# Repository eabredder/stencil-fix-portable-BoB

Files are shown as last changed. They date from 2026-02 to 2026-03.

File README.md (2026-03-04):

# **Stencil Fix Portable — BoB v.03 - PCB**

A purpose-built **drop‑in PCB** for the **Stencil Fix Portable** vacuum stencil holder. This board replaces the original perfboard wiring with a compact, repeatable assembly, eliminating soldering any wires using common connectors using an **Adafruit QtPy SAMD21 (QtPy M0)**, a **B10K potentiometer** for vacuum control, a **128×32 SSD1306 OLED** for status, and a **30A ESC** driving an **A2212 BLDC motor**. The CAD files in this repository are updated to fit these changes. You can still use this with the original Stencil Fix Portable design and components, you may need to adjust the range of motor control (µs), arming procedure, without the OLED. The PCB outline is 80mm x 20mm, matching common perfboard layout and mounting.

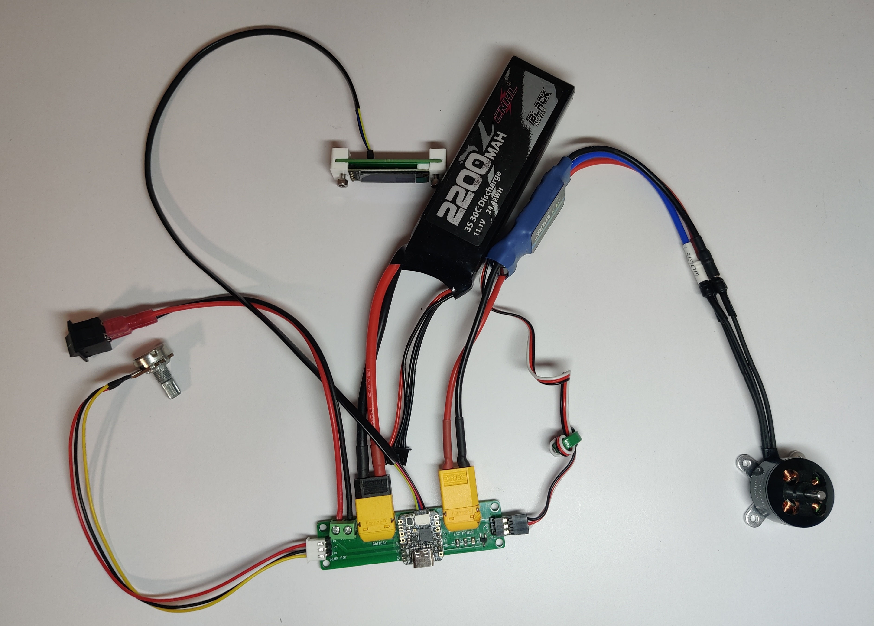
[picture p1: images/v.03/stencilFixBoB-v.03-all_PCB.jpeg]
StencilFix BoB v.03 Connected Components


<!--![StencilFix BoB v.03 3D View](images/v.03/3DView-Components-v.03.png)-->

This project is intended to be used with the original Stencil Fix Portable mechanical design and overall concept from the upstream project: [**Stencil Fix Portable** by scheffield](https://github.com/scheffield/stencil-fix-portable). Our updates reflect using more commonly sourced hardware, simplifying the build, and lower cost components. See BOM for updated components and design decisions.

---

## **Highlights / Features**

- **Drop-in replacement PCB** for the Stencil Fix Portable electronics
- **Cooperative Multitasking** providing simple scheduler and tasks using [TaskScheduler](https://github.com/arkhipenko/TaskScheduler)
- [**QtPy SAMD21** microcontroller](https://github.com/adafruit/Adafruit-QT-Py-PCB/blob/master/README.md)
- **Vacuum control** via 10K potentiometer → mapped to ESC PWM (servo µs)
- **5V input from ESC**: 
-  - No need for buck-boost
-  - BAT54 Diode protection
- **OLED UI (128×32 SSD1306)**:
  - Vacuum % bar
  - Battery % bar (with low/critical blinking label)
  - Fan state (ON/OFF)
  - Auto **screen dim after 30 seconds** inactivity
- **Battery SoC estimation** via voltage divider (scaled for **3S LiPo**)
- **Input smoothing** using a one-pole low-pass filter (reduces “twitchy” response)
- **Onboard NeoPixel UX**:
  - Arming/breathing animation
  - Hue reflects potentiometer
  - Low-battery dimming
  - Critical-battery blink
- **XT60 Connectors** standardized connections for RC batteries and ESCs, reduce connector/wiring inside
- **Power Switch** simplified through screw terminals
- **80x20mm Outline**  with 3.2mm Mounting Holes to fit multiple screw types and heat set threaded inserts and drop-in to original design

---

## **Hardware Overview**

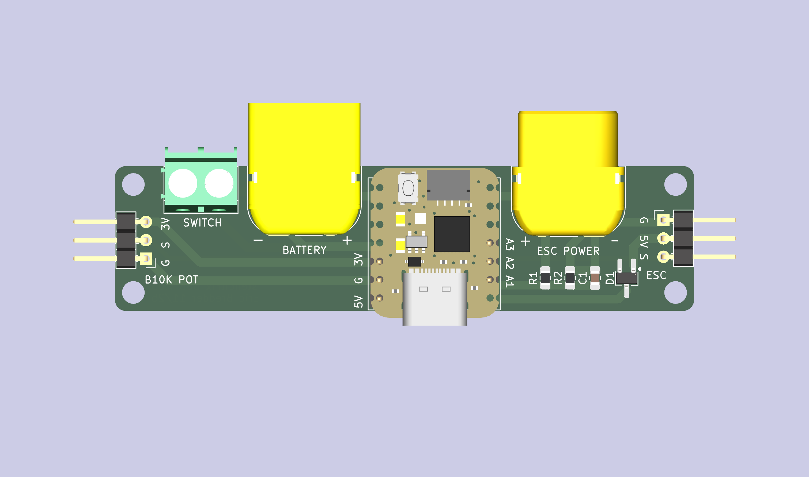
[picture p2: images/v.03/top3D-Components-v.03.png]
 

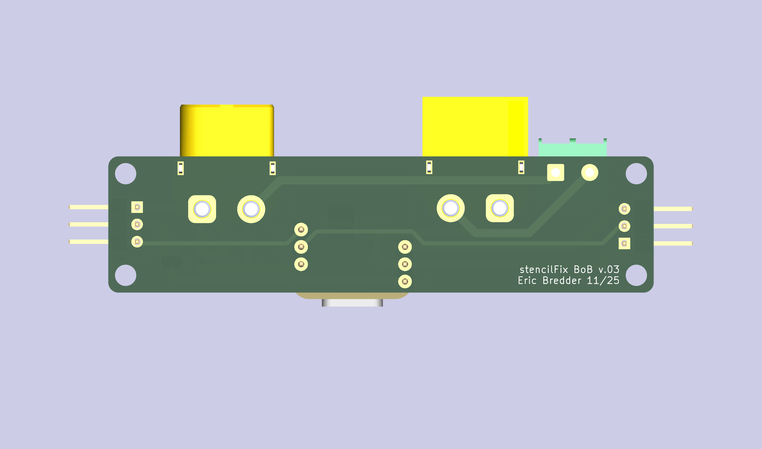
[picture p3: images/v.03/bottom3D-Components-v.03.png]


### **PCB Components**
- MCU
  - U1: [Adafruit QtPy SAMD21 (QtPy M0)](https://www.adafruit.com/qtpy)
- Battery sense & filtering
  - R1: [300kΩ 0805 Resistor](https://a.co/d/0bcWREO8)
  - R2: [100kΩ 0805 Resistor](https://a.co/d/0bcWREO8)
  - C1: [100nF 0805 Capacitor](https://a.co/d/0i44cuZE)
- Protection
  - D1: [BAT54 Schottky Diode SOT-23-3](https://a.co/d/0dFgMzRd)
- Connectors
  - J5, ESC Power: [XT60 Male](https://a.co/d/0fRPskBY)
  - J2, ESC UBEC: [2.54mm Male Right Angle](https://a.co/d/08ONmiCH) - 3 pin
  - J3, Battery: [XT60 Female](https://a.co/d/0fRPskBY)
  - J4, Power Switch: [5.08mm Screw Terminal Block](https://a.co/d/0d4A6ITm) - 2 pin
  - J1, Potentiometer: [2.54mm Male Right Angle](https://a.co/d/08ONmiCH) - 3 pin
  - U1, MCU Header: [2.54 Male Straight](https://a.co/d/08ONmiCH) - 3 pin (2x)
    
### **External Hardware**
- Control: [B10K (10KΩ) Linear Potentiometer](https://a.co/d/0iVrtQ9j)
- Motor: [A2212 1400kV BLDC Motor](https://a.co/d/0cnJZqye)
- ESC: [30A ESC with 5V BEC](https://a.co/d/0eS2Lal8)
- Battery: [3S LiPo (nominal 11.1V, max 12.6V)](https://a.co/d/00FffIhA)
- Switch: [SPST - 19.2mm x 12.7mm](https://a.co/d/03Vc4zIX)
- Display: 128×32 SSD1306 I2C OLED (0x3C): [OLED Only (Solder or add backpack)](https://a.co/d/053kOUIJ) OR [Adafruit 4440 (Stemma QT)](https://www.adafruit.com/product/4440)
- Wire (better for switch): [18AWG Silicone Wire](https://a.co/d/00WXGGEn)
- Qwiic/Stemma QT Cable (for display): [200mm Stemma QT Cable](https://www.adafruit.com/product/4401) OR [150mm Stemma QT w/ Headers Cable](https://www.adafruit.com/product/4209)

### **Charging**
- Extension cable: [200mm JST-XH Balance Plug Extension](https://a.co/d/07cr4UUC)
- LiPo Charger: [B3 Balance Charger - 3S XH3P Plug](https://a.co/d/02X7mcL8)

## **Electrical Design Notes**

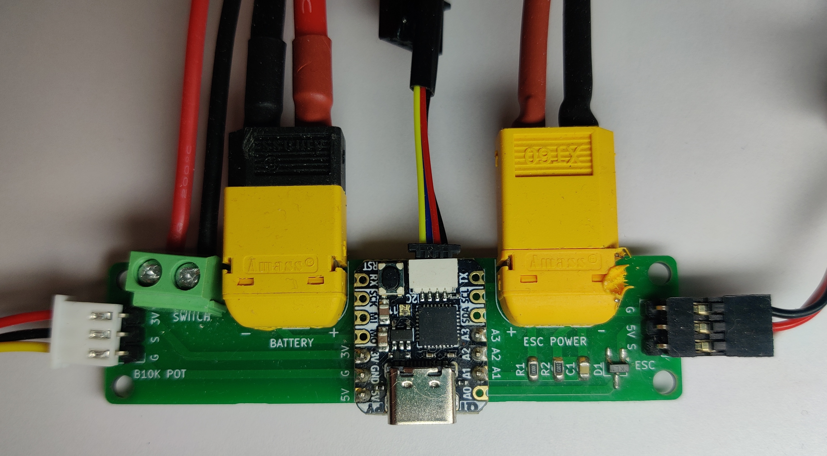
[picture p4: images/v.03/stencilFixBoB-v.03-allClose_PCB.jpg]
StencilFix BoB v.03 3D View


### **Schematic**
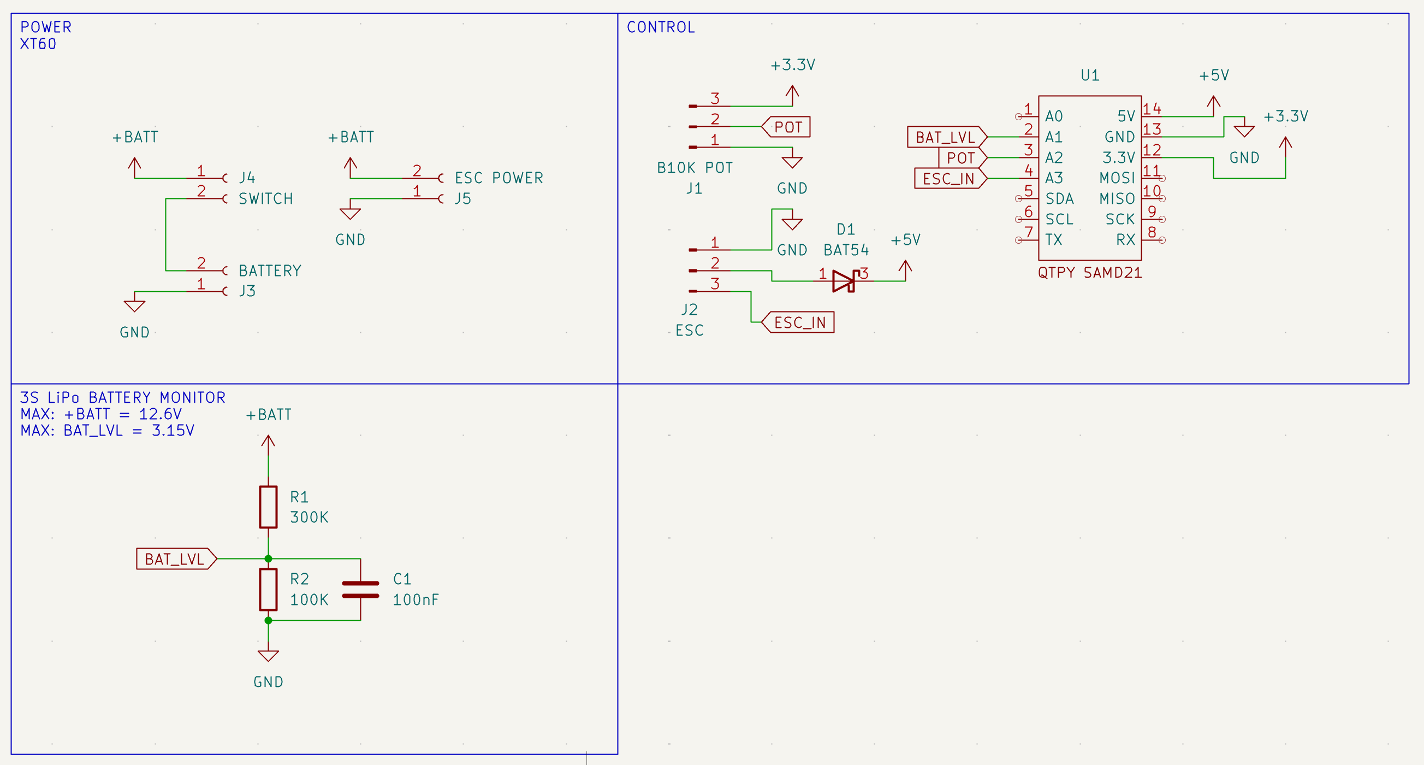
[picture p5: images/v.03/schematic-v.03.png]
StencilFix BoB v.03 KiCad Schematic


### **3S LiPo Battery Monitor/Filter (safe for 3.3V ADC)**

**R1** = 300kΩ, **R2** = 100kΩ
```text
R2 / (R1 + R2) = 100kΩ / 400kΩ = 0.25
```

So at 12.6V max, ADC max voltage:
```text
12.6V × 0.25 = 3.15V
```

**C1** = 100nF (from BAT_LVL to GND as simple RC filter)

### **ESC 5V Protection (Schottky diode)**
**D1** = BAT54 Schottky diode on the ESC’s 5V UBEC rail - used to prevent reverse-current/back-powering conditions between supplies. Expect a small forward voltage drop, typically a few hundred mV depending on load.

### **Connectors / Wiring**

**J3** — BATTERY (XT60, female on PCB) - Connect 3S LiPo here

**J5** — ESC POWER (XT60, male on PCB) - Connect ESC power input here

**J4** — SWITCH (2-pin screw terminal block) - Inline with the battery positive path (rocker switch pigtails)

**J2** — ESC (3-pin)
- ESC_IN PWM signal to ESC (servo µs)
- +5V from ESC UBEC (through diode to board +5V rail)
- GND

**J1** — B10K POT (3-pin)
- 3.3V
- POT, wiper input
- GND

**I2C OLED**
- SDA / SCL from the QtPy STEMMA QT Connector
- Address: 0x3C
- Power: 3.3V

### **SAMD21 Pin Mapping**

| **Pin**  | **MCU Function** | **Schematic** | **Notes** |
|---|---|---|---|
| A1 | Battery Level Input | BAT_LVL | 3.15V Max Voltage Divider for Battery SoC |
| A2 | Potentiometer Input | POT | 12-bit ADC Potentiometer Scaled Input for Control |
| A3 | PWM Signal Output | ESC_IN | PWM Output for ESC Control |
| 5V | 5V Power In | +5V | 5V Power Input from Schottky Diode/ESC UBEC |
| GND  | Ground | GND | Common Ground |
| 3.3V | 3.3V Power Out | +3.3V | 3.3V Power Output for Potentiometer and OLED |

Uses PIN_NEOPIXEL [(built-in QtPy NeoPixel support)](https://learn.adafruit.com/adafruit-qt-py/neopixel-blink)

## **Firmware Notes**
**ESC arming**

On boot, ESC is held at 1000 µs for 2 seconds, then control is enabled. While not armed, NeoPixel shows an amber “breathing” animation.

**Pot → PWM mapping**

ADC reads at 12-bit (0..4095), Mapped to 1100..1400 µs (then low-pass filtered), If filtered value < 1110 µs, output floors to 1000 µs (fan off), Vacuum % shown as: 1100..1400 µs → 0..100%

**Display**

Vac bar with % (top row), Bat bar with % (second row, “Bat” blinks at low/critical), Bottom row: Fan: ON/OFF, Screen dims after 30 seconds of inactivity and wakes on pot movement or fan state change.

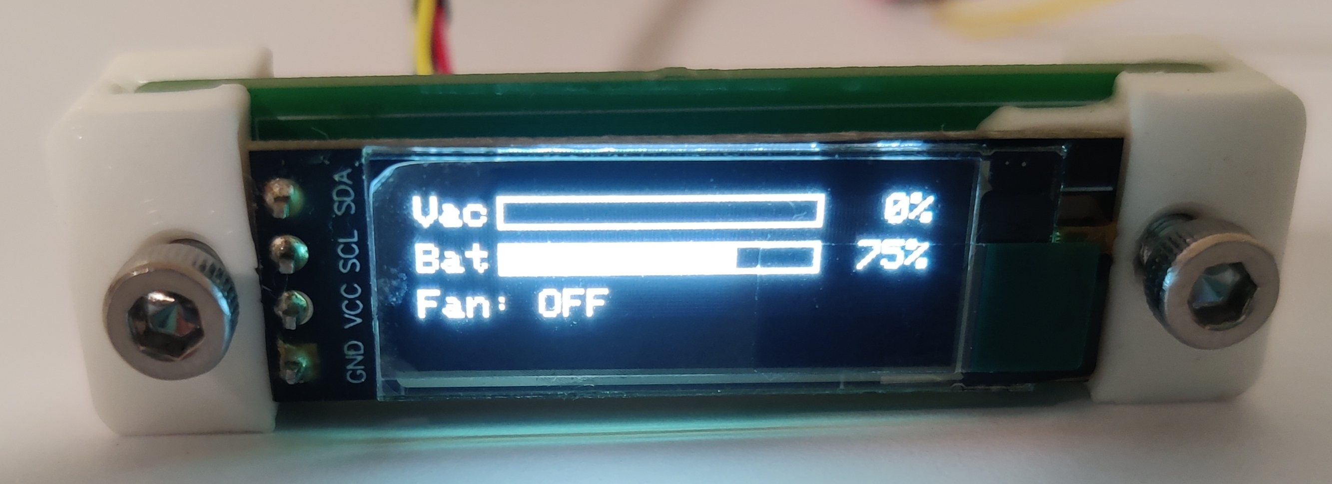
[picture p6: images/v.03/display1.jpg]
StencilFix BoB v.03 Display Off
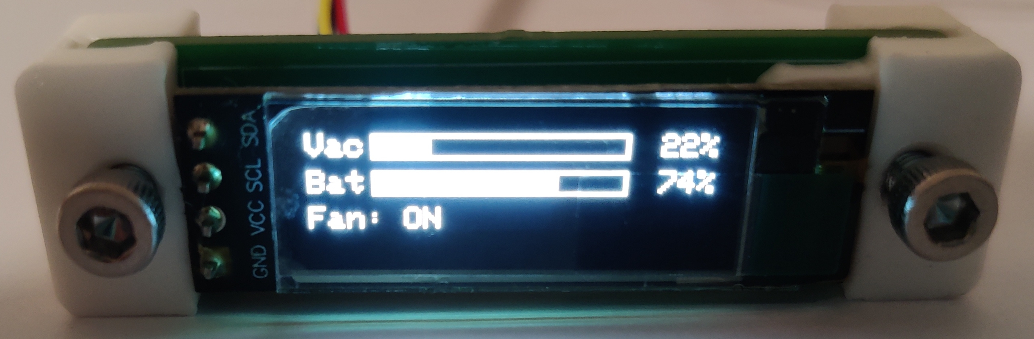
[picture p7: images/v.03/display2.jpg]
StencilFix BoB v.03 Display On
  

**Battery**

Battery SoC % computed and smoothed with moving averages:
```text
vmin = 9.0V
vmax = 12.6V
```

### **Arduino Libraries**
**Community**:
- [TaskScheduler](https://github.com/arkhipenko/TaskScheduler)
- [Adafruit_NeoPixel](https://github.com/adafruit/Adafruit_NeoPixel)
- [Servo](https://github.com/arduino-libraries/Servo)
- [Adafruit_GFX](https://github.com/adafruit/Adafruit-GFX-Library)
- [Adafruit_SSD1306](https://github.com/adafruit/Adafruit_SSD1306)
- [movingAvg](https://github.com/JChristensen/movingAvg/tree/master)

**Included**:
- lib/BatteryMeter.h [adapted from ESP Battery Shield](https://github.com/inf0matics/esp-battery-shield/tree/main/lib/BatteryMeter)

### **Attribution / Inspiration**

Stencil Fix Portable upstream project by scheffield (mechanical + concept reference). [Stencil Fix Portable](https://github.com/scheffield/stencil-fix-portable)

Battery meter approach referenced from ESP-Battery-Shield by inf0matics (voltage divider / ADC math concept). [ESP Battery Shield](https://github.com/inf0matics/esp-battery-shield/tree/main/lib/BatteryMeter)

**License:** [GNU General Public License v3.0](https://www.gnu.org/licenses/gpl-3.0.en.html)

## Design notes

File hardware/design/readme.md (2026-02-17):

[4600 QTPy.step - Adafruit](https://github.com/adafruit/Adafruit_CAD_Parts/tree/main/4600%20QT%20Py)

[AMASS XT60PW Connectors -  Anton Kolomeytsev](https://grabcad.com/library/xt60pw-and-xt60-dc-connectors-1)

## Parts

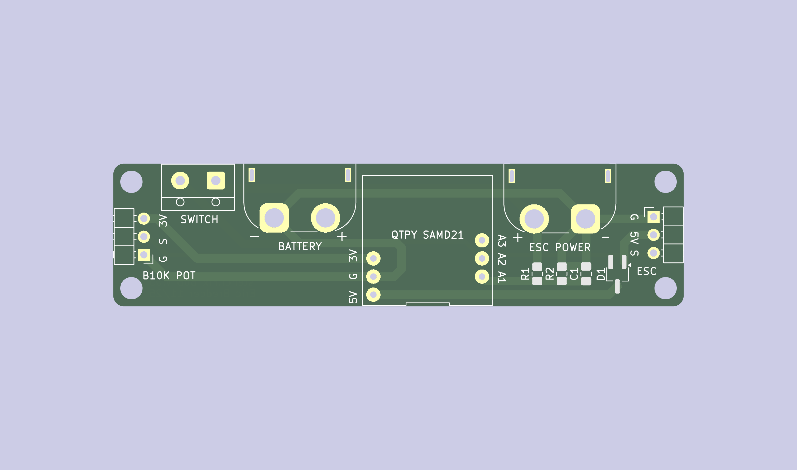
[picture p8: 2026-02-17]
images/v.03/top3D-noComponents-v.03.png

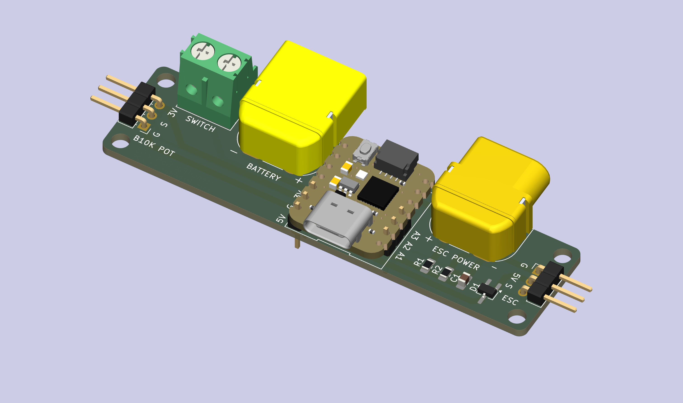
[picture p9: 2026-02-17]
images/v.03/3DView-Components-v.03.png

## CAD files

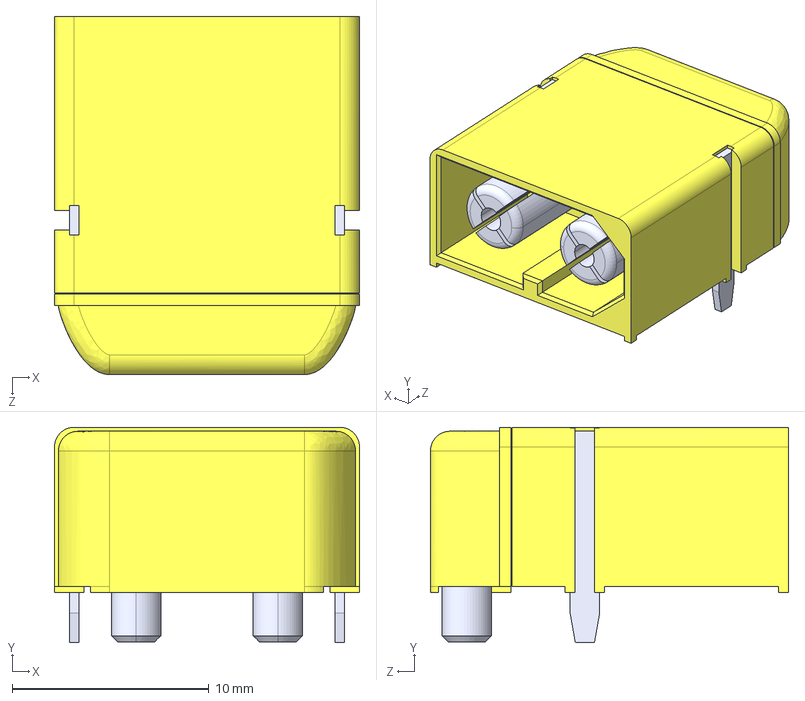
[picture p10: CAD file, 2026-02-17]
hardware/design/XT60PW-M--3DModel-STEP-269445.STEP
15.5 x 11.0 x 18.2 mm

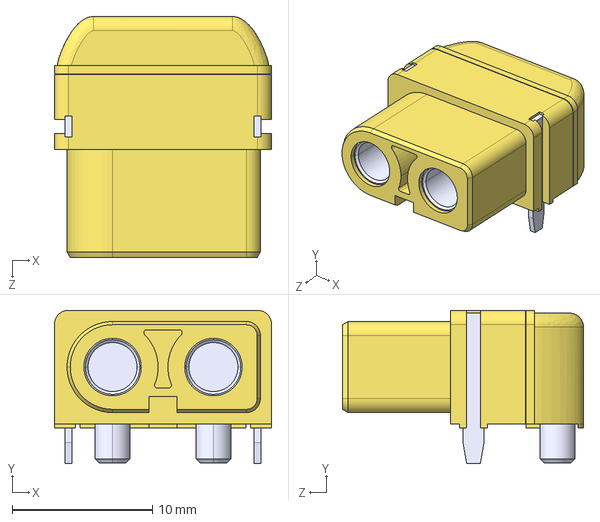
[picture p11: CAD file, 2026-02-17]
hardware/design/XT60PW-F--3DModel-STEP-510211.STEP
15.5 x 10.9 x 17.2 mm

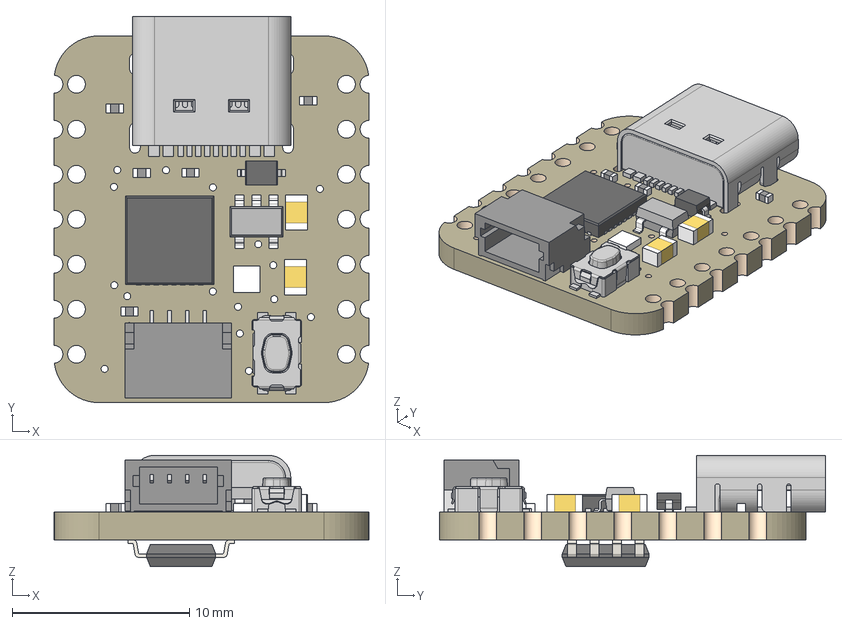
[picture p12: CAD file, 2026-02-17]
hardware/design/4600 QTPy.step
17.8 x 21.8 x 6.28 mm
Board
10uF x 2
reset
ATSAMD21E
TPB1,27
5.1K x 5
USB TYPE C
STEMMA_I2C_QTSKINNY
AP2112K-3.3
WS2812B_SK6805_1515
NSR0320
SOIC8_150MIL

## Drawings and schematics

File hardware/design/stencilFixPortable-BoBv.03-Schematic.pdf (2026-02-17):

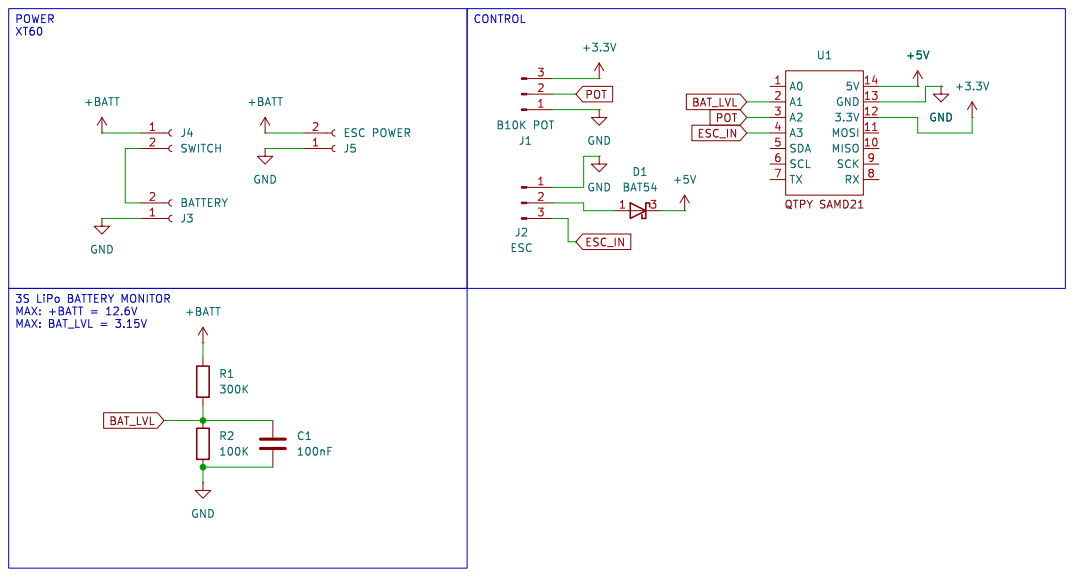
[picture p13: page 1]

+BATT GND J4SWITCH J5ESC POWER 2 1 J3BATTERY 1

3S LiPo BATTERY MONITOR MAX: +BATT = 12.6V MAX: BAT_LVL = 3.15V

Id: 1/1 Title: Stencil Fix Portable - BoB

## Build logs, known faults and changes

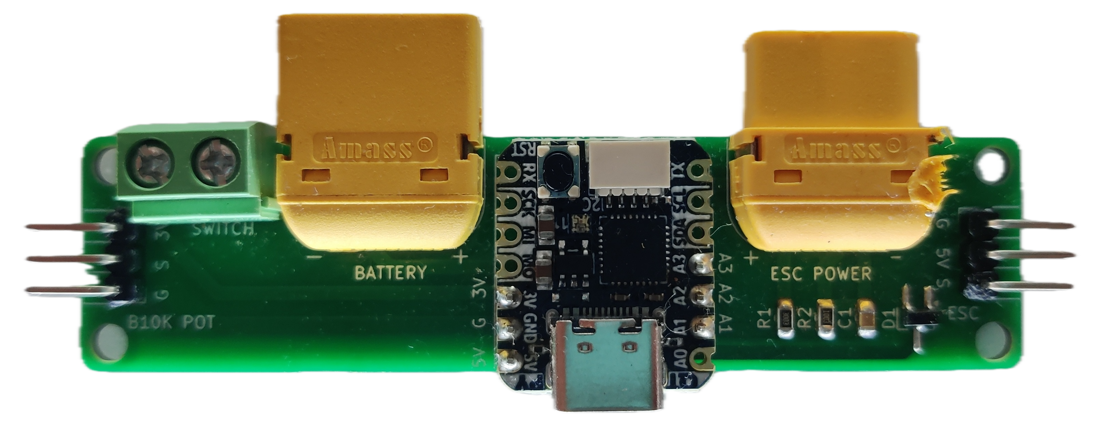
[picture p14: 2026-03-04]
images/v.03/stencilFixBoB-v.03-componentsTop_PCB.png

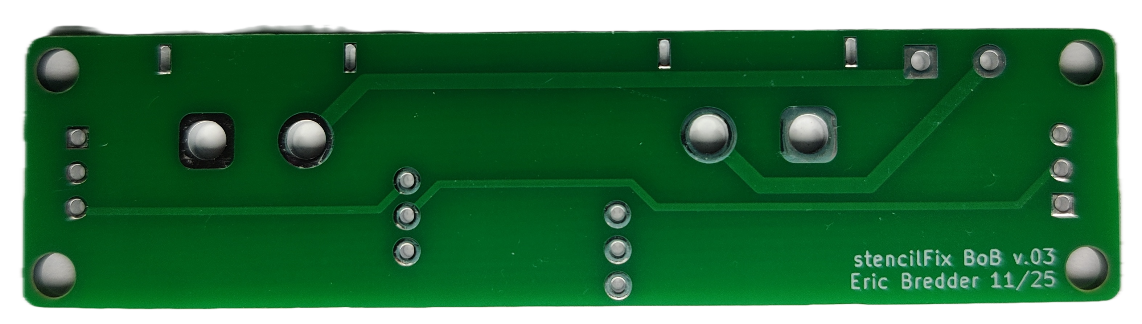
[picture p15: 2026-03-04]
images/v.03/stencilFixBoB-v.03-bottom_PCB.png

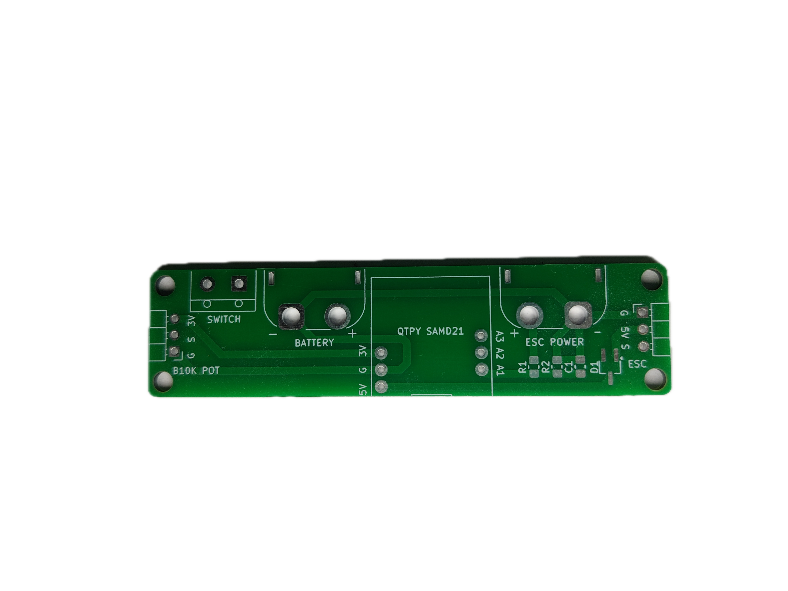
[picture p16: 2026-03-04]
images/v.03/stencilFixBoB-v.03-top_PCB.png

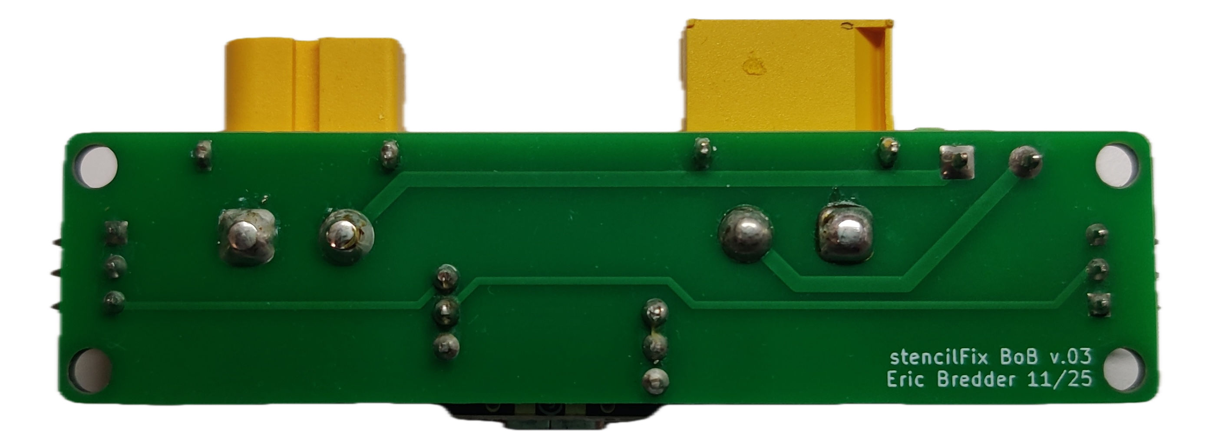
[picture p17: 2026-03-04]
images/v.03/stencilFixBoB-v.03-allBottom_PCB.png

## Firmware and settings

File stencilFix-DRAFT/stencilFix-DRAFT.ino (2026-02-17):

// ==== Battery meter from https://github.com/thespielplatz/esp-battery-shield ====

#include <Arduino.h>
#include <TaskScheduler.h>

#include <Adafruit_NeoPixel.h>
#include <Servo.h>

// Display
#include <Wire.h>
#include <Adafruit_GFX.h>
#include <Adafruit_SSD1306.h>

// Sensors
#include "BatteryMeter.h"
#include <movingAvg.h>

// ---------------------- Low-pass filter ----------------------
class LowPass {
  public:
    explicit LowPass(float RCus) : _RCus(RCus) {}
    float step(float x) {
      unsigned long now = micros();
      if (_lastMicros == 0) {
        _lastMicros = now;
        _y = x;
        return _y;
      }
      unsigned long dt = now - _lastMicros; // microseconds
      _lastMicros = now;
      // Standard one-pole: alpha = dt / (RC + dt)
      float alpha = (float)dt / (_RCus + (float)dt);
      _y += alpha * (x - _y);
      return _y;
    }
    void reset(float x) {
      _y = x;
      _lastMicros = micros();
    }
  private:
    float _y = 0.0f;
    float _RCus;                 // time constant in microseconds
    unsigned long _lastMicros = 0;
};

// ---------------------- OLED ----------------------
#define SCREEN_WIDTH 128
#define SCREEN_HEIGHT 32
#define SCREEN_ADDRESS 0x3C
Adafruit_SSD1306 display(SCREEN_WIDTH, SCREEN_HEIGHT, &Wire);

// ---------------------- Battery ----------------------
movingAvg avgBatt(22);
const int batteryPin = A1;
const float R1 = 300000.0;
const float R2 = 100000.0;
const float vmin = 9.0;
const float vmax = 12.6;
BatteryMeter* batteryMeter = new BatteryMeter(R1, R2, batteryPin, vmin, vmax);

// ---------------------- NeoPixel ----------------------
#define NUMPIXELS 1
Adafruit_NeoPixel pixels(NUMPIXELS, PIN_NEOPIXEL, NEO_GRB + NEO_KHZ800);

// ----- Onboard NeoPixel power & brightness policy -----
const uint8_t BRIGHT_ARMED   = 32;  // arming animation
const uint8_t BRIGHT_NORMAL  = 24;  // default after arming
const uint8_t BRIGHT_LOW     = 10;  // low battery dim
const uint8_t BRIGHT_CRIT    = 4;   // critical battery dim/blink
const int     BATT_LOW_PCT   = 25;  // thresholds for dimming
const int     BATT_CRIT_PCT  = 10;  // thresholds for blinking

// ---------------------- Servo / ESC ----------------------
Servo servo;

// ---------------------- Pins ----------------------
const int potPin   = A2;   // potentiometer
const int servoPin = A3;   // ESC signal (QtPy M0 supports this)

// ---------------------- Filters & State ----------------------
// Original RC = 40us; for stronger smoothing try 50–150ms (e.g., 100000 us).
LowPass lowPass(100000.0f);

// Shared state
volatile int      g_rawPot       = 0;      // 0..4095
volatile int      g_servoUs      = 1100;   // clamped microseconds for ESC
volatile int      g_vacuumPct    = 0;      // 0..100
volatile int      g_battPct      = 0;      // 0..100
volatile float    g_battVoltage  = 0.0f;   // volts
volatile uint16_t g_pixelHue     = 0;      // 0..65535
volatile bool     g_escArmed     = false;  // becomes true after arming delay

// ---------- Screen Dimming ----------
unsigned long lastActivityTime = 0;
const unsigned long screenDimTimeout = 30000;  // 30 seconds
bool screenDimmed = false;

// ---------------------- Scheduler ----------------------
Scheduler runner;

// ---------- Forward declarations ----------
void taskReadInputsCb();
void taskServoCb();
void taskPixelCb();
void taskBatteryCb();
void taskDisplayCb();
void taskSerialCb();
void taskArmEscCb();

void drawBar(int x, int y, int width, int height, int pct);
void printRightAligned(const String& s, int xRight, int y);
bool blinkState(unsigned long periodMs);

// Periods — responsive but light
Task taskReadInputs (5   /*ms*/, TASK_FOREVER, &taskReadInputsCb, &runner, false);
Task taskServo      (10  /*ms*/, TASK_FOREVER, &taskServoCb     , &runner, false);
Task taskPixel      (20  /*ms*/, TASK_FOREVER, &taskPixelCb     , &runner, false);
Task taskBattery    (250 /*ms*/, TASK_FOREVER, &taskBatteryCb   , &runner, false);
Task taskDisplay    (200 /*ms*/, TASK_FOREVER, &taskDisplayCb   , &runner, false);
Task taskSerial     (1000/*ms*/, TASK_FOREVER, &taskSerialCb    , &runner, false);

// Non-blocking ESC arming (hold 1000us for 2s, then allow control)
Task taskArmEsc     (2000/*ms*/, TASK_ONCE,   &taskArmEscCb     , &runner, false);

// ---------------------- Setup ----------------------
void setup() {
  Serial.begin(115200); // SAMD21 handles higher baud nicely

  // SAMD21 ADC: 12-bit range 0..4095
  analogReadResolution(12);

  // Display
  if (!display.begin(SSD1306_SWITCHCAPVCC, SCREEN_ADDRESS)) {
    Serial.println(F("SSD1306 allocation failed"));
    for(;;) { /* stop here if OLED not present */ }
  }
  display.clearDisplay();
  display.setTextColor(SSD1306_WHITE, SSD1306_BLACK);
  display.setRotation(0);
  display.display();

  // Battery smoothing
  avgBatt.begin();

  // Onboard NeoPixel (QtPy M0 has PIN_NEOPIXEL; NEOPIXEL_POWER may or may not exist)
  #if defined(NEOPIXEL_POWER)
    pinMode(NEOPIXEL_POWER, OUTPUT);
    digitalWrite(NEOPIXEL_POWER, HIGH);
  #endif
  pixels.begin();
  pixels.setBrightness(BRIGHT_NORMAL); // start conservative
  pixels.clear();
  pixels.show();

  // IO
  pinMode(potPin, INPUT);
  pinMode(batteryPin, INPUT);

  // Servo / ESC
  servo.attach(servoPin, 1100, 1900); // SAMD21 Servo lib works on this pin

  // Initialize the low-pass to the current mapped value to avoid a jump
  int pot0 = analogRead(potPin);
  int initialUs = map(pot0, 0, 4095, 1100, 1400);
  lowPass.reset(initialUs);

  // Initialize activity timer & full brightness
  lastActivityTime = millis();
  screenDimmed = false;
  display.ssd1306_command(SSD1306_SETCONTRAST);
  display.ssd1306_command(255);

  // Start tasks
  taskReadInputs.enable();
  taskServo.enable();
  taskPixel.enable();
  taskBattery.enable();
  taskDisplay.enable();
  taskSerial.enable();

  // Start non-blocking ESC arming
  taskArmEsc.enable(); // after 2000ms it will set g_escArmed = true
}

// ---------------------- Loop ----------------------
void loop() {
  runner.execute(); // cooperative dispatcher
}

// ---------------------- Helper drawing & UI functions ----------------------

// Generic compact progress bar
void drawBar(int x, int y, int width, int height, int pct) {
  pct = constrain(pct, 0, 100);
  display.drawRect(x, y, width, height, SSD1306_WHITE);
  int fillWidth = map(pct, 0, 100, 0, width - 2);
  if (fillWidth > 0) {
    display.fillRect(x + 1, y + 1, fillWidth, height - 2, SSD1306_WHITE);
  }
}

// Right-align small text (size=1) to an xRight column
void printRightAligned(const String& s, int xRight, int y) {
  // Each character at size=1 is ~6px wide in the default GFX font
  int textWidth = s.length() * 6;
  int x = xRight - textWidth + 1;  // +1 to balance outline pixels
  if (x < 0) x = 0;
  display.setCursor(x, y);
  display.print(s);
}

// Non-blocking blink state helper
bool blinkState(unsigned long periodMs) {
  return (millis() / periodMs) % 2 == 0;
}

// ---------------------- Task Callbacks ----------------------

// Sample pot, LPF, compute servo µs and vacuum %
void taskReadInputsCb() {
  int pot = analogRead(potPin);   // 12-bit on SAMD21
  g_rawPot = pot;

  // Map pot to 1100..1400us target, then low-pass
  int targetUs = map(pot, 0, 4095, 1100, 1400);
  int filtered = (int) lowPass.step((float)targetUs);

  // Original behavior: floor to 1000 if <1110
  if (filtered < 1110) filtered = 1000;

  // Clamp safe ESC range
  filtered = constrain(filtered, 1000, 1400);
  g_servoUs = filtered;

  // Vacuum percentage from 1100..1400 → 0..100
  int pct = map(filtered, 1100, 1400, 0, 100);
  g_vacuumPct = constrain(pct, 0, 100);

  // ---------- Inactivity detection for screen dimming ----------
  static int  lastPot    = -1;
  static bool lastFanOn  = false;
  bool fanOn = (g_vacuumPct > 0 && g_escArmed);

  if (pot != lastPot || fanOn != lastFanOn) {
    lastActivityTime = millis();
    if (screenDimmed) {
      // Restore brightness immediately on activity
      display.ssd1306_command(SSD1306_SETCONTRAST);
      display.ssd1306_command(255);  // full brightness
      screenDimmed = false;
    }
  }
  lastPot   = pot;
  lastFanOn = fanOn;
}

// Drive the servo/ESC (respect arming)
void taskServoCb() {
  int outUs = g_escArmed ? g_servoUs : 1000;
  servo.writeMicroseconds(outUs);
}

// Onboard NeoPixel policy:
// - Critical battery: red blink (1 Hz)
// - Not armed: breathing amber
// - Armed: hue by pot (240°..360°), brightness dimmed on low battery
void taskPixelCb() {
  uint32_t now = millis();

  // Critical battery: slow red blink (1 Hz, 500ms on/500ms off)
  if (g_battPct <= BATT_CRIT_PCT) {
    bool on = ((now / 500) % 2) == 0;
    pixels.setBrightness(BRIGHT_CRIT);
    if (on) {
      pixels.fill(pixels.Color(255, 0, 0)); // solid red
    } else {
      pixels.clear();
    }
    pixels.show();
    return;
  }

  // ESC not yet armed: amber "breathing" (triangular wave)
  if (!g_escArmed) {
    // 1500 ms triangle wave: 0..255..0
    const uint16_t period = 1500;
    uint16_t t = now % period;
    uint8_t wave = (t < period / 2)
                     ? map(t, 0, period / 2, 10, 200)
                     : map(t, period / 2, period, 200, 10);

    pixels.setBrightness(BRIGHT_ARMED);
    // Amber-ish (HSV ≈45°): RGB ~ (255, 80, 0), scaled by 'wave'
    uint8_t r = (uint8_t)(255UL * wave / 255UL);
    uint8_t g = (uint8_t)( 80UL * wave / 255UL);
    uint8_t b = 0;
    pixels.fill(pixels.Color(r, g, b));
    pixels.show();
    return;
  }

  // Armed & running: hue reflects potentiometer and brightness depends on battery
  uint8_t bright = (g_battPct <= BATT_LOW_PCT) ? BRIGHT_LOW : BRIGHT_NORMAL;
  pixels.setBrightness(bright);

  // Hue: 240°..360° → 43690..65535 in 16-bit hue space
  uint16_t hueStart = (uint16_t)(65535UL * 240UL / 360UL); // 43690
  uint16_t hue = (uint16_t)map(g_rawPot, 0, 4095, (int)hueStart, 65535);

  pixels.fill(pixels.ColorHSV(hue, 255, 255));
  pixels.show();
}

// Read/smooth battery data
void taskBatteryCb() {
  BatteryMeter::BatteryData d = batteryMeter->getBatteryData();
  g_battVoltage = d.batteryVoltage;

  int p = avgBatt.reading(d.percentage);
  g_battPct = constrain(p, 0, 100);
}

// ======= DISPLAY: Option B3 (Grid) with W1 bars (80 px wide) =======
void taskDisplayCb() {
  // ---------- Screen Dimming Logic ----------
  unsigned long now = millis();
  if (!screenDimmed && (now - lastActivityTime > screenDimTimeout)) {
    // Dim the display
    display.ssd1306_command(SSD1306_SETCONTRAST);
    display.ssd1306_command(10);  // dim level (0–255)
    screenDimmed = true;
  }

  if (screenDimmed) {
    // Minimal message while dimmed (fast exit to save cycles)
    display.clearDisplay();
    display.setTextSize(1);
    display.setCursor(22, 12);
    display.print(F("Display dimmed"));
    display.display();
    return;
  }

  display.clearDisplay();
  display.setTextSize(1); // uniform, compact

  // --- Layout constants for B3 ---
  const int barX       = 20;  // left edge of both bars
  const int barWidth   = 80;  // W1 width
  const int barHeight  = 8;   // compact & uniform
  const int vacY       = 0;   // row 1 top
  const int batY       = 12;  // row 2 top
  const int rightCol   = 127; // right edge for right-aligned text

  // ---------- Row 1: Vacuum ----------
  display.setCursor(0, vacY);
  display.print(F("Vac"));
  drawBar(barX, vacY, barWidth, barHeight, g_vacuumPct);

  {
    // Right-aligned "%": e.g., "42%"
    char buf[8];
    snprintf(buf, sizeof(buf), "%d%%", g_vacuumPct);
    printRightAligned(String(buf), rightCol, vacY);
  }

  // ---------- Row 2: Battery (Blink 'Bat' when low/critical) ----------
  bool lowBatt  = (g_battPct <= 20);
  bool critBatt = (g_battPct <= 10);

  // Blink rate: 1Hz for low, 2Hz for critical
  bool showBat = true;
  if (critBatt)      showBat = blinkState(500);
  else if (lowBatt)  showBat = blinkState(1000);

  if (showBat) {
    display.setCursor(0, batY);
    display.print(F("Bat"));
  }
  drawBar(barX, batY, barWidth, barHeight, g_battPct);

  {
    // Right-aligned "%": e.g., "78%"
    char buf[8];
    snprintf(buf, sizeof(buf), "%d%%", g_battPct);
    printRightAligned(String(buf), rightCol, batY);
  }

  // ---------- Bottom row: Fan state ----------
  const bool fanOn = (g_vacuumPct > 0 && g_escArmed);
  display.setCursor(0, 24);
  display.print(F("Fan: "));
  display.print(fanOn ? F("ON") : F("OFF"));

  display.display();
}

// Serial telemetry
void taskSerialCb() {
  Serial.println(F("Potentiometer microseconds:"));
  Serial.println(g_servoUs);
  Serial.println();

  Serial.println(F("Battery %:"));
  Serial.println(g_battPct);
  Serial.println();

  Serial.println(F("Battery Voltage:"));
  Serial.println(g_battVoltage, 3);
  Serial.println();
}

// One-shot arming completion after 2s
void taskArmEscCb() {
  g_escArmed = true;
}
